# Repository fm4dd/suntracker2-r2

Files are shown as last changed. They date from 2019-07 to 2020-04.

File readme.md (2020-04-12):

# SunTracker2 Revision 2



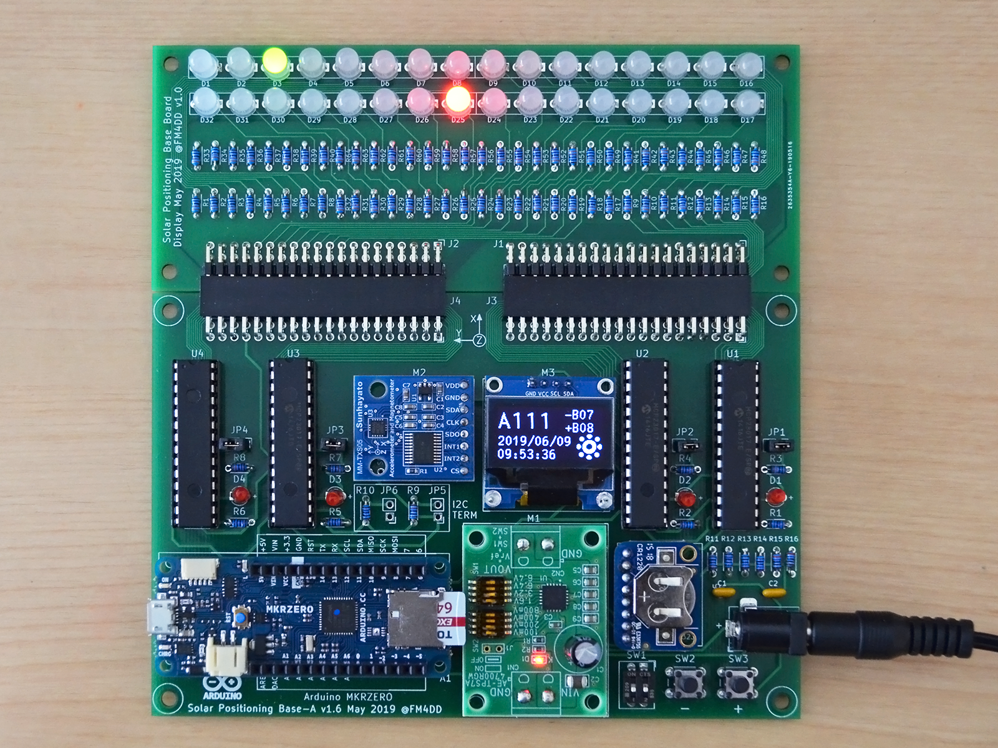
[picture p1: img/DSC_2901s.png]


This project develops a photovoltaic (PV) solar tracking controller.
Pictured above is the revision 2 prototype. PV solar trackers control the PV
panel direction to keep the panel perpendicular to the Sun, maximizing the
power output. The power output difference for a fully aligned panel is
reported to be in a range of 15~40%, which would be substantial.

## Design

The goal is a self-orienting dual-axis, scheduled, Arduino-based solar
tracker. I want to control PV panel orientation for both Elevation and
Azimuth angles (dual-axis), based on the calculated solar position of a PV
systems specific geographic location and time (scheduled).

Working under space, cost and time constraints, the prototype development is
done on a small scale model. Eventually, I want to control and optimize the
orientation of Mini-PV systems.

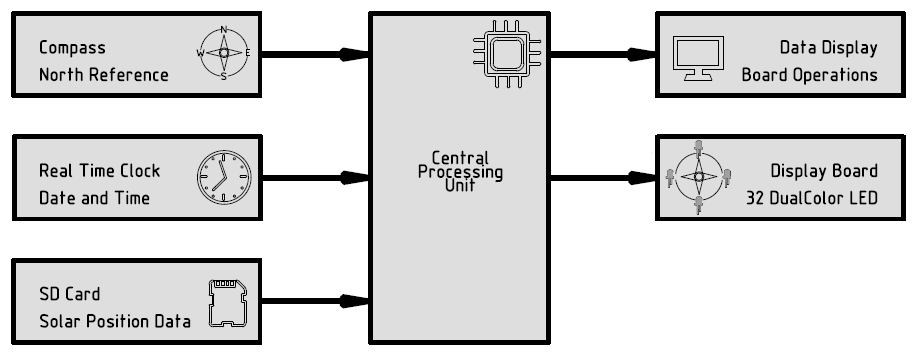
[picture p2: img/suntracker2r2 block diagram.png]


This is a interim revision to establish PCB design and manufacturing. The next
version is revision 3, located <a href="https://github.com/fm4dd/suntracker2-r3">here</a>

### Board Description and Components

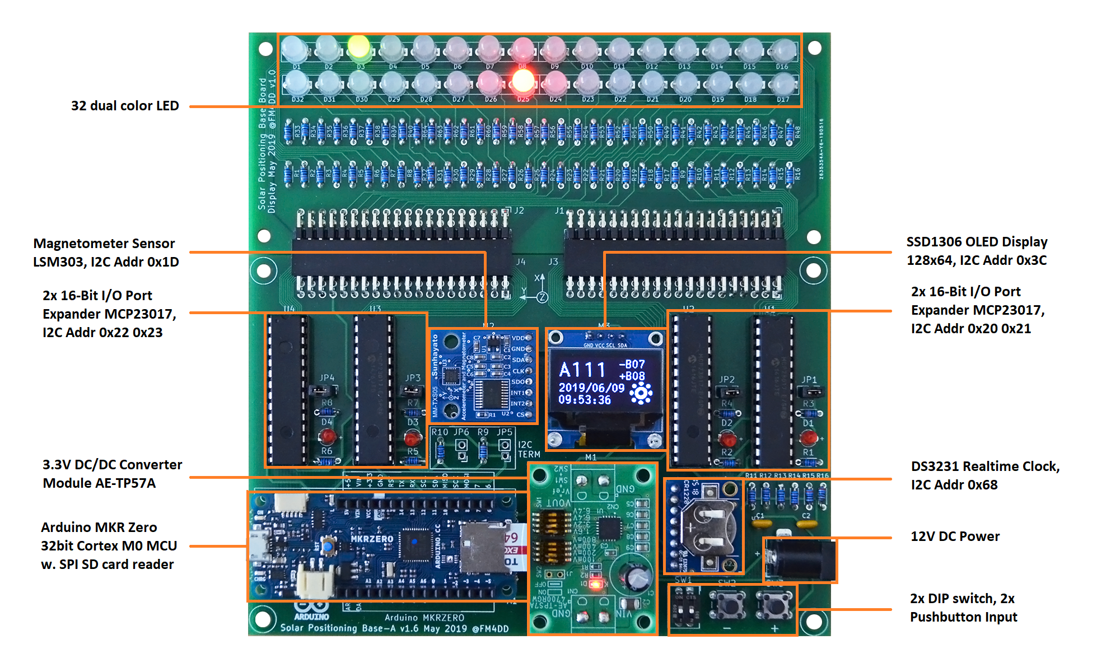
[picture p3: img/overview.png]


The main controller board contains the 32bit Arduino MKRZero MCU, the
LSM303 magnetometer sensor, DS3231 RTC clock module, and four 16pin GPIO expander
circuits. A 128x64 OLED display shows operational data and status messages.

A 32-color LED display board connects to the controller board to develop the 
GPIO controller functions for the sun positioning display.

In the next revision, the 32 LED ring will form a ring that represents the horizon
with north, sunrise and sunset indicators, and a green indicator to display the
suns daily movement over time.

The solar position data gets calculated off-system in advance, and saved into a
micro SD card. The pre-generated daily sun position files are then read by the
Arduino MKR Zero microcontroller through the onboard card reader. The
astronomical calculations of the suns position require sufficient CPU power, and
are taxing on Microcontrollers.

At the moment I am using a sun position dataset that covers two years of
operation, and uses approx. 20MB in size (46 MB with additional debug data). I
wrote the “suncalc” tool to pre-calculate the data set files for a specific
location, on a Linux PC.

### PCB

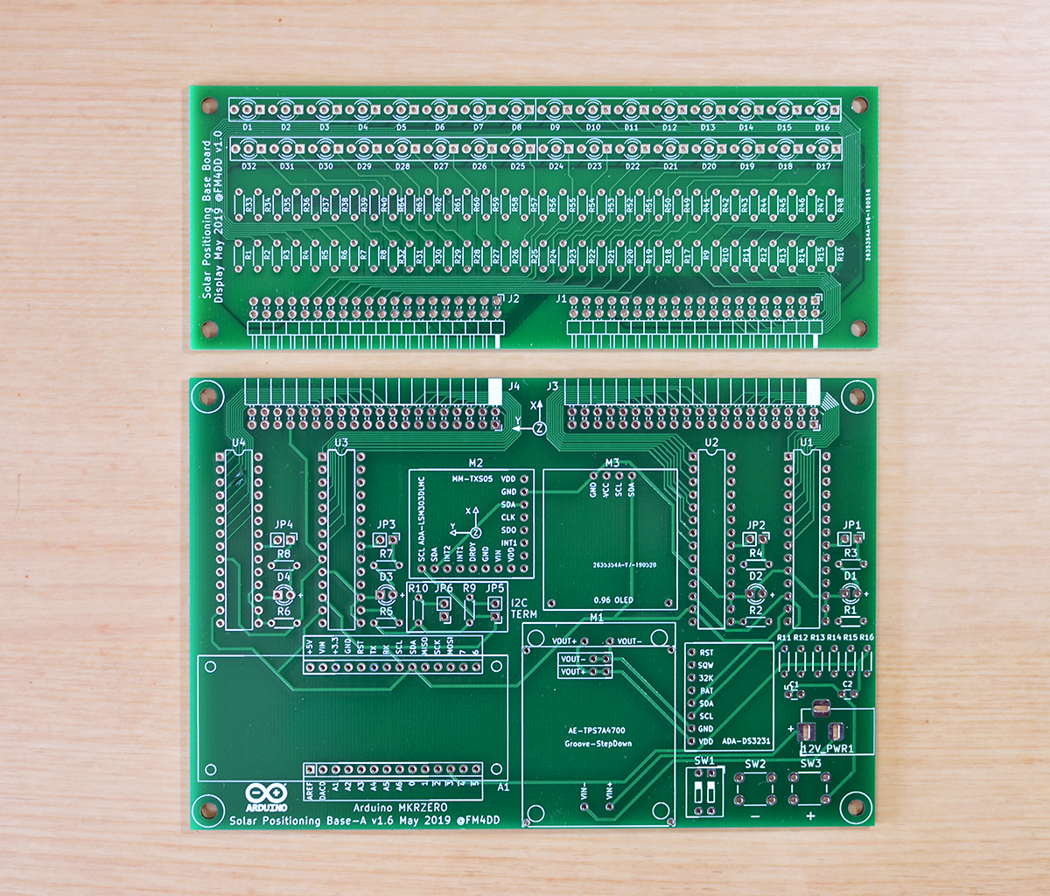
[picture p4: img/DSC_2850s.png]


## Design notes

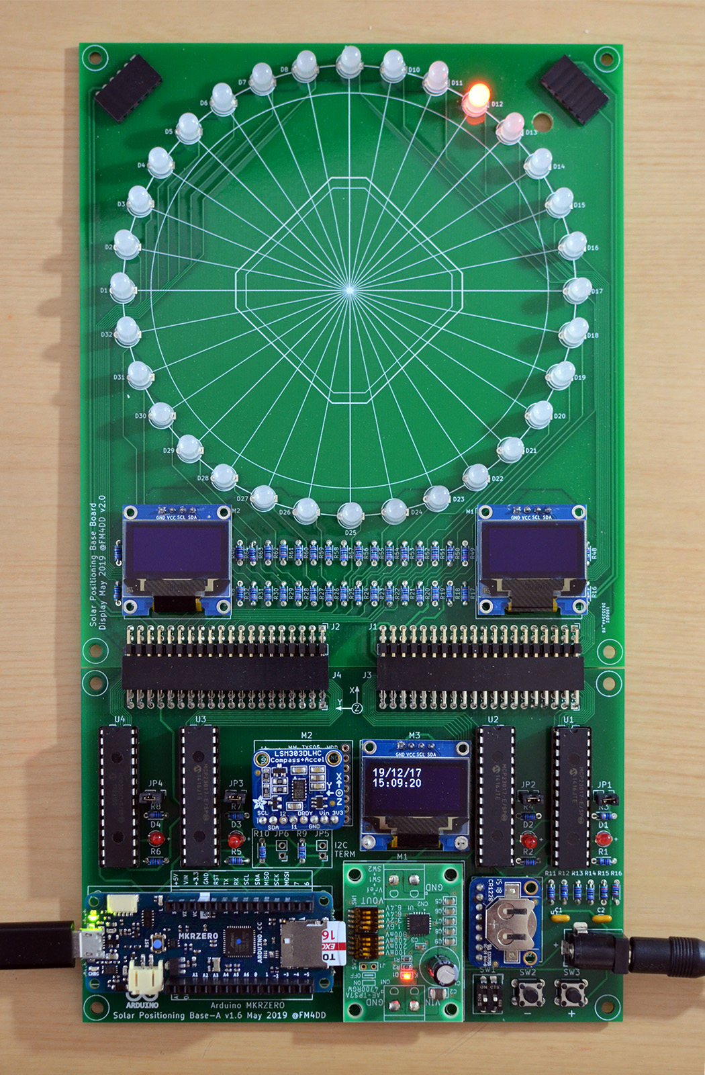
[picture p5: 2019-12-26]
img/displayv2-on-mbv16.jpg

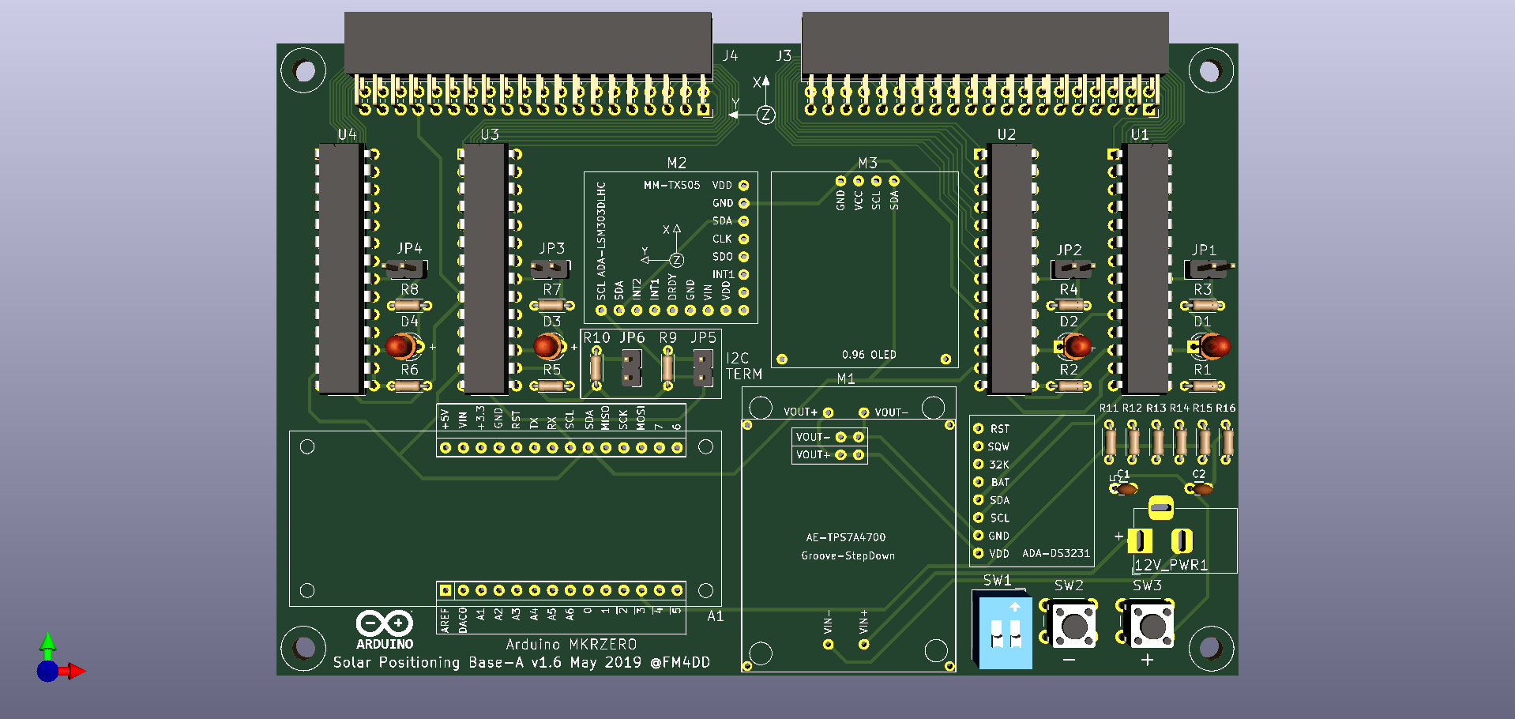
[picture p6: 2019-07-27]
img/mainboard v1.6.png

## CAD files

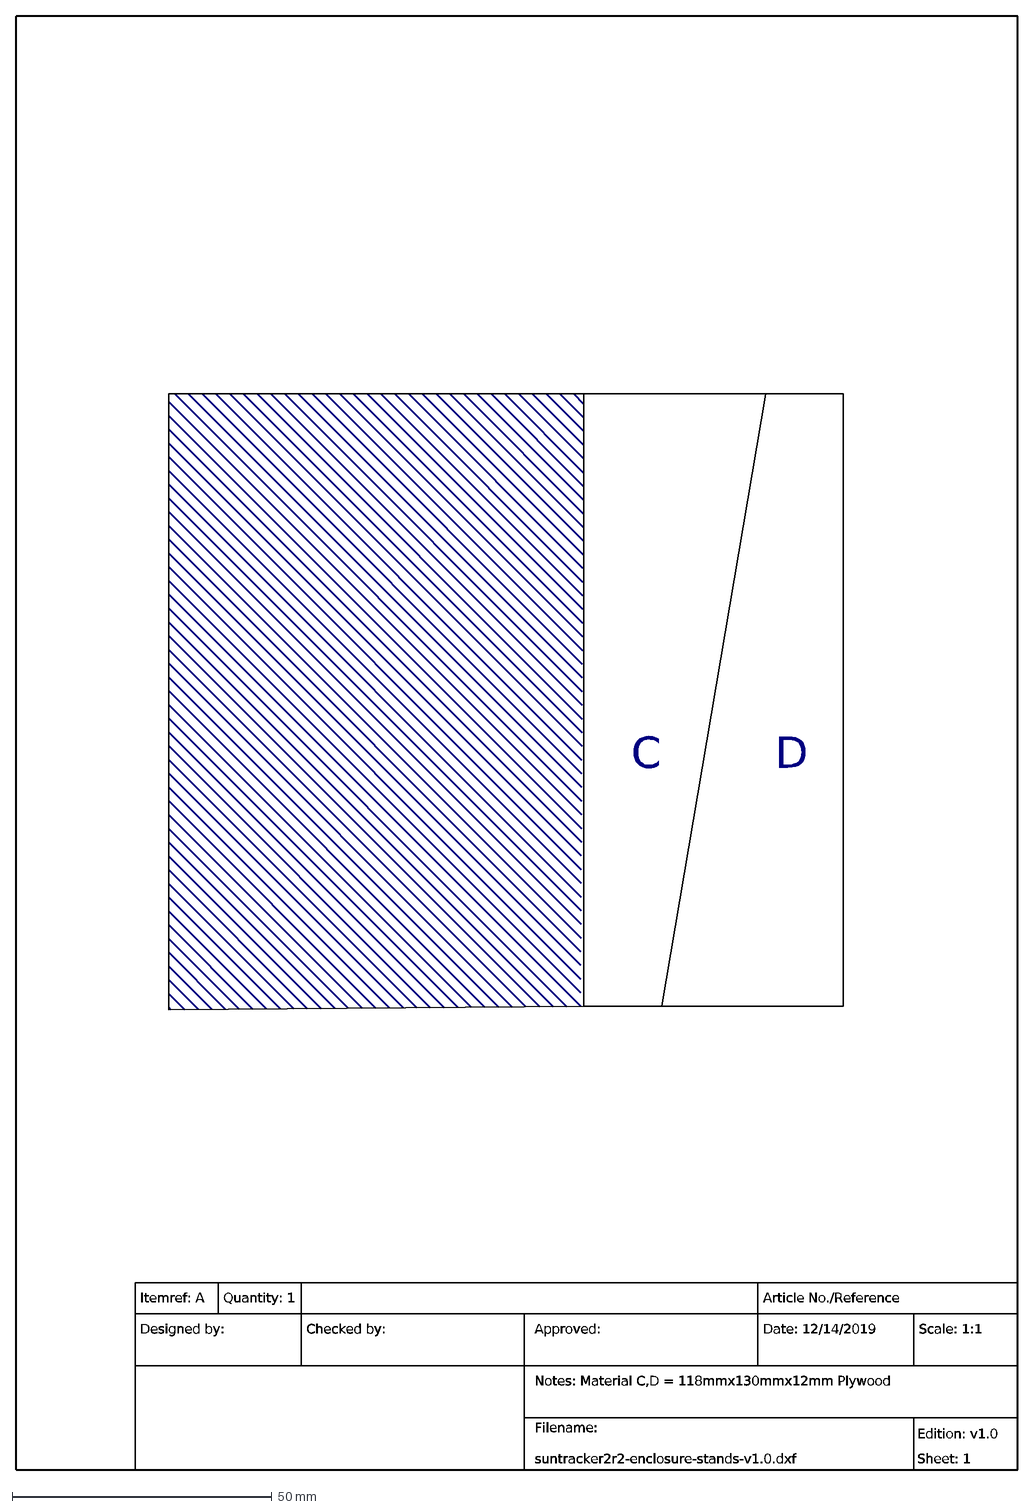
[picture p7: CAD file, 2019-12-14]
doc/20191214 suntracker2r4-enclosure-stands-v1.0.dxf
Notes: Material C,D = 118mmx130mmx12mm Plywood
Itemref: A
Quantity: 1
Article No./Reference
Designed by:
Checked by:
Approved:
Filename: suntracker2r2-enclosure-stands-v1.0.dxf
Date: 12/14/2019
Scale: 1:1
Edition: v1.0 Sheet: 1
C
D

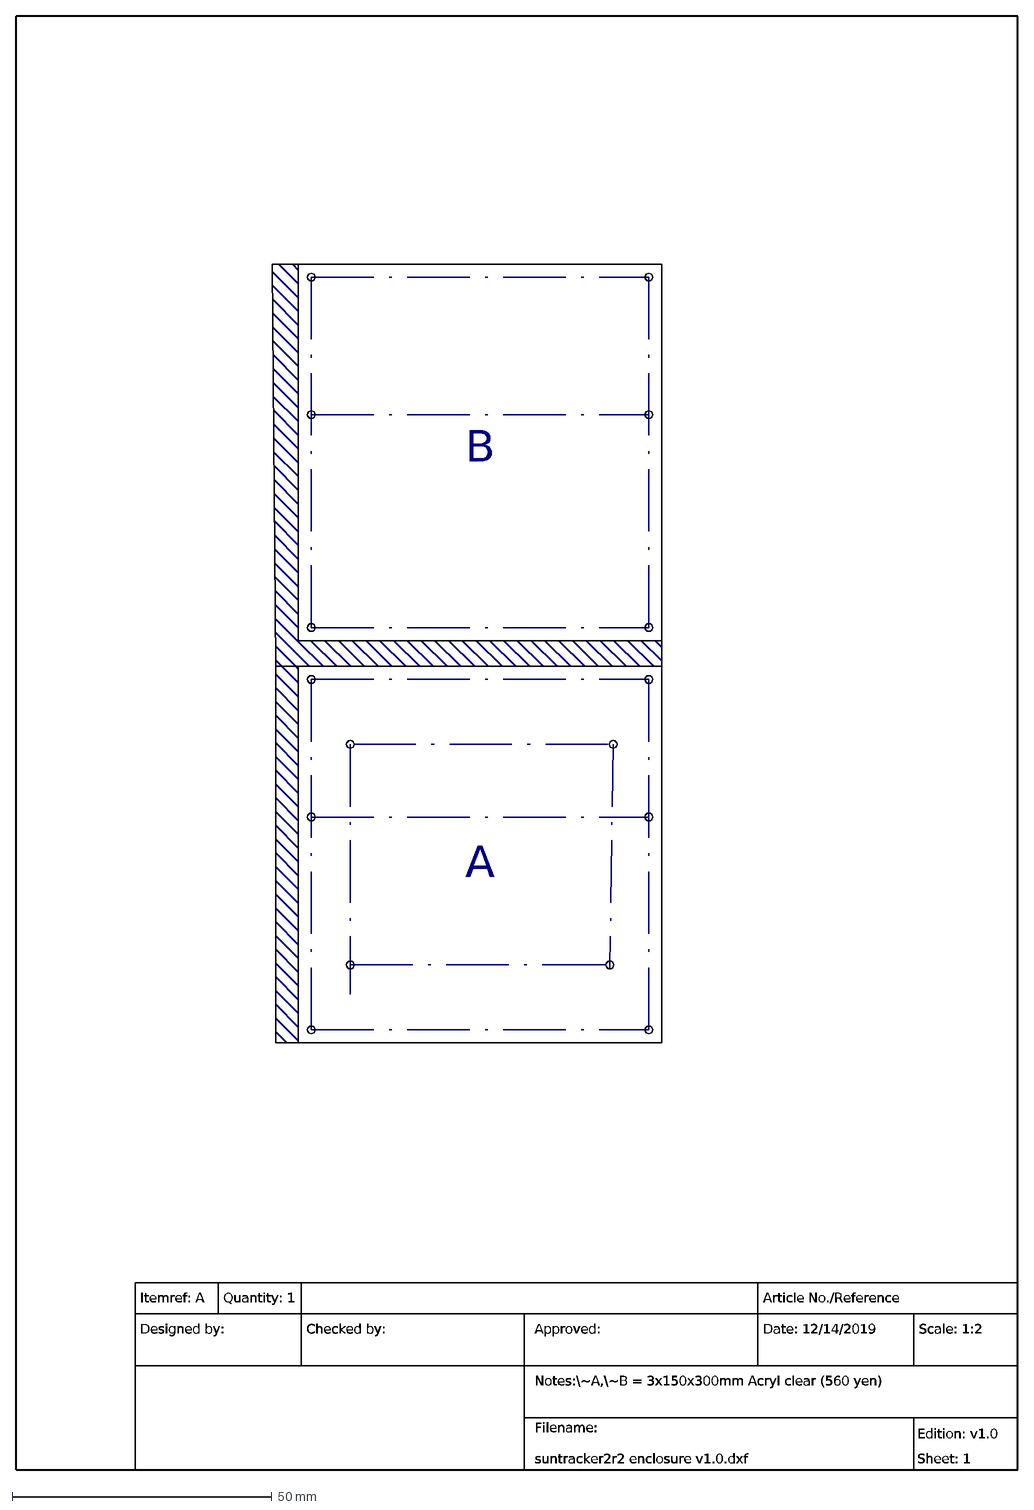
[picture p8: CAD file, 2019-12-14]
doc/20191214 Suntracker2r2 enclosure v1.0.dxf
Notes:\~A,\~B = 3x150x300mm Acryl clear (560 yen)
Itemref: A
Quantity: 1
Article No./Reference
Designed by:
Checked by:
Approved:
Filename: suntracker2r2 enclosure v1.0.dxf
Date: 12/14/2019
Scale: 1:2
Edition: v1.0 Sheet: 1
A
B

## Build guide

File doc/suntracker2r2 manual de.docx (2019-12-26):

Das Suntracker2R2 ist eine 32-bit Arduino MKR Zero basierte Mikroprozessor Entwicklungsumgebung zur Ansteuerung von 64 digitalen I/O. Damit kann man zum Beispiel eine Displayboard Erweiterung mit 32x Zweifarben-LED zur Datenausgabe ansteuern. Als Eingangsdaten steht eine Echtzeituhr (RTC), ein Magnetometer Sensor, und der MicroSD Kartenleser des Arduino MKR Zero zur Verfuegung. Ein 128x64 OLED Display dient zur Zustands-, Daten und Messwertausgabe.

## Board Design


## Komponenten Uebersicht

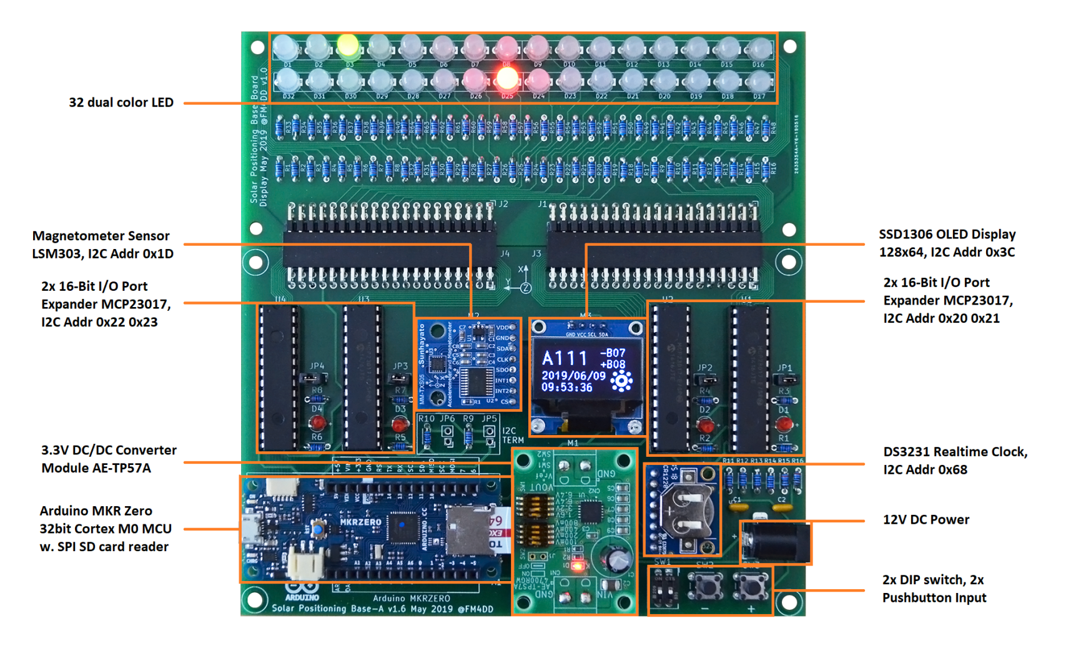
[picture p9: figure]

Below tables show some of the DE0-Nano-SOC’s basic built-in HW components: LED, Pushbutton, DIP, and Clock.

LED | FPGA PIN | | Push Button | FPGA PIN | | DIP Switch | FPGA PIN
LED[0] | PIN_W15 | | KEY[0] | PIN_AH17 | | DIP Switch[0] | PIN_L10
LED[1] | PIN_AA24 | | KEY[1] | PIN_AH16 | | DIP Switch[1] | PIN_L9
LED[2] | PIN_V16 | | | | | DIP Switch[2] | PIN_H6
LED[3] | PIN_V15 | | Clock | FPGA PIN | | DIP Switch[3] | PIN_H5
LED[4] | PIN_AF26 | | FPGA_CLK1_50 | PIN_V11
LED[5] | PIN_AE26 | | FPGA_CLK2_50 | PIN_Y13
LED[6] | PIN_Y16
LED[7] | PIN_AA23 | | Pushbutton keys are level “high”, and go “low” when pressed.
| | | DIP switches are level “high” in down position, and “low” when up.

## Arduino MKR Zero

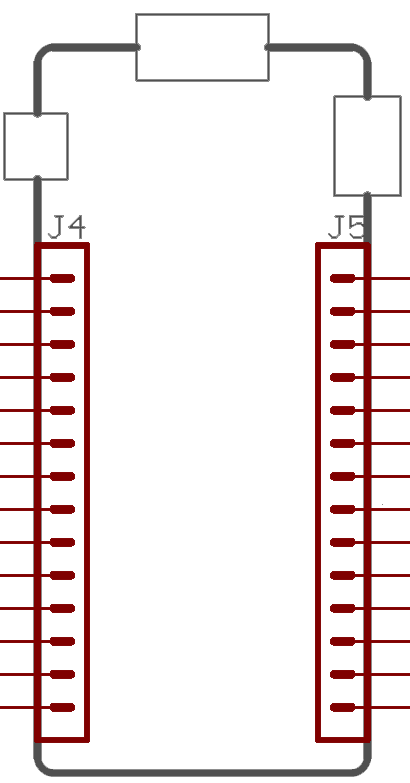
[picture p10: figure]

Herzstück des Boards ist der Arduino MKR Zero, eine Cortex M0 basierte 32bit CPU mit 32K RAM und 256K Flash Speicher.

I/O Header Pin Belegungsplan:

Am Arduino sind 8 Pins belegt,

und 20 von 28 Pins ungenutzt.

Board Pin | Arduino Pin | # | | # | Arduino Pin | Board Pin
N/A | AREF | 1 | | 28 | +5V | N/A
N/A | DAC0 | 2 | | 27 | VIN | N/A
N/A | A1 | 3 | | 26 | +3.3V | DC Converter +
N/A | A2 | 4 | | 25 | GND | DC Converter -
N/A | A3 | 5 | | 24 | RESET | N/A
N/A | A4 | 6 | | 23 | 14 | N/A
N/A | A5 | 7 | | 22 | 13 | N/A
N/A | A6 | 8 | | 21 | SCL | I2C Bus Clock
DIP Switch 0 | 0 | 9 | | 20 | SDA | I2C Bus Data
DIP Switch 1 | 1 | 10 | | 19 | 10 | N/A
Taster 1 (SW2) | 2 | 11 | | 18 | 9 | N/A
Taster 2 (SW3) | 3 | 12 | | 17 | 8 | N/A
N/A | 4 | 13 | | 16 | 7 | N/A
N/A | 5 | 14 | | 15 | 6 | N/A

## DIE DIp Schalter und Taster (Default OFF = 1, ON = 0)

Das Board ist mit zwei DIP Schaltern und zwei Tastern ausgestattet. Diese können zur Steuerung von Programmen und Ausgaben frei belegt werden. Der folgende Demo Sketch s2r2-dipkey-test.ino zeigt die Ansteuerung:

/* ------------------------------------------------- */

/* Suntracker2R2 DIP and Pushbutton Test Sketch */

/* ------------------------------------------------- */

#include "Arduino.h" // default library

#define DIP1 0 // dip switch 1 <-> IO-pin 0

#define DIP2 1 // dip switch 2 <-> IO-pin 1

#define KEY1 2 // pushbutton 1 <-> IO-pin 2

#define KEY2 3 // pushbutton 2 <-> IO-pin 3

uint8_t dippos1 = 1; // dip switch 1 position

uint8_t dippos2 = 1; // dip switch 2 position

uint8_t push1 = 1; // pushbutton 1 position

uint8_t push2 = 1; // pushbutton 2 position

void setup() {

Serial.begin(115200);

while (!Serial); // wait for serial port to connect.

Serial.println("Serial OK");

/* ------------------------------------------------- */

/* Set dip switch and push button IO pins for input */

/* ------------------------------------------------- */

pinMode(DIP1, INPUT);

pinMode(DIP2, INPUT);

pinMode(KEY1, INPUT);

pinMode(KEY2, INPUT);

pinMode(push1, INPUT);

pinMode(push2, INPUT);

Serial.println("DIP and KEY pins set for input.");

}

void loop() {

/* ------------------------------------------------- */

/* Get and display dip switch and pushbutton status */

/* ------------------------------------------------- */

Serial.print(" DIP1: "); dippos1 = digitalRead(DIP1); Serial.print(dippos1);

Serial.print(" DIP2: "); dippos2 = digitalRead(DIP2); Serial.print(dippos2);

Serial.print(" KEY1: "); push1 = digitalRead(KEY1); Serial.print(push1);

Serial.print(" KEY1: "); push2 = digitalRead(KEY2); Serial.print(push2);

Serial.println();

delay(500);

}

Die Ausgabe erfolgt hier über den seriellen Monitor der Arduino IDE. Dieser sollte in der Arduino IDE gestartet werden, sonst beginnt das Program nicht. Hier ist ein Beispiel-Screenshot der seriellen Ausgabe:

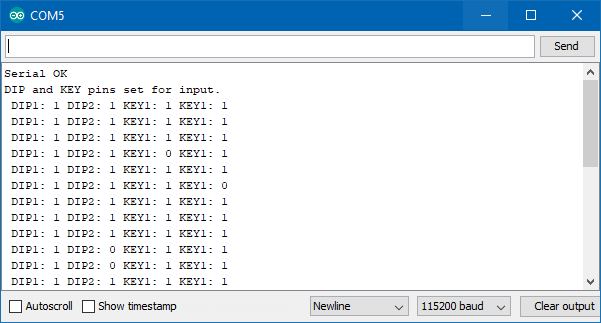
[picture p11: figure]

- Beachte die invertierte Logik: Ein Tastendruck oder Switch-ON generiert ein ‘0’ Signal.

## Der I2C BUS

Auf dem Mainboard verbindet der I2C Bus die acht folgenden Geraete mit der Arduino MCU:

# | Geraet | Typ | Hersteller | I2C Bus Addresse (Hex)

1 | Accelerometer | LSM303DLHC | Adafruit | 0x19
2 | Magnetometer | See above | See above | 0x1E
3 | IO Expander 1 | MCP23017 E/SP | Microchip | 0x20
4 | IO Expander 2 | MCP23017 E/SP | Microchip | 0x21
5 | IO Expander 3 | MCP23017 E/SP | Microchip | 0x22
6 | IO Expander 4 | MCP23017 E/SP | Microchip | 0x23
7 | OLED Display | SSD1306 | Unbranded | 0x3C
8 | RTC Clock | DS3231 | Adafruit | 0x68

Der Demo Sketch s2r2-i2cscan-test.ino ueberprüft, ob alle Gerate am I2C Bus gefunden werden:

/* ------------------------------------------------- */

/* Suntracker2R2 12C Bus Scanner Test Sketch */

/* ------------------------------------------------- */

#include <Wire.h> // Arduino built-in I2C bus function library

uint8_t error = 0; // I2C commuications error

uint8_t address = 0; // I2C device address

uint8_t counter = 0; // I2C device counter

void setup(){

Serial.begin(115200);

while (!Serial); // wait for serial port to connect.

Serial.println("Serial OK. Scanning I2C Bus:");

Wire.begin(); // enable I2C bus, default speed

for(address = 0; address < 127; address++ ) {

Serial.print(".");

Wire.beginTransmission(address);

error = Wire.endTransmission();

if (error == 0){

Serial.print("\nDevice found: 0x");

Serial.println(address,HEX);

counter++;

continue;

}

if (error == 4) {

Serial.print("\nDevice error: 0x");

Serial.println(address,HEX);

continue;

}

delay(100);

}

Serial.print("\n I2C bus scan result: ");

Serial.print(counter);

Serial.print(" devices found.");

}

void loop() {}

Serielle Ausgabe:

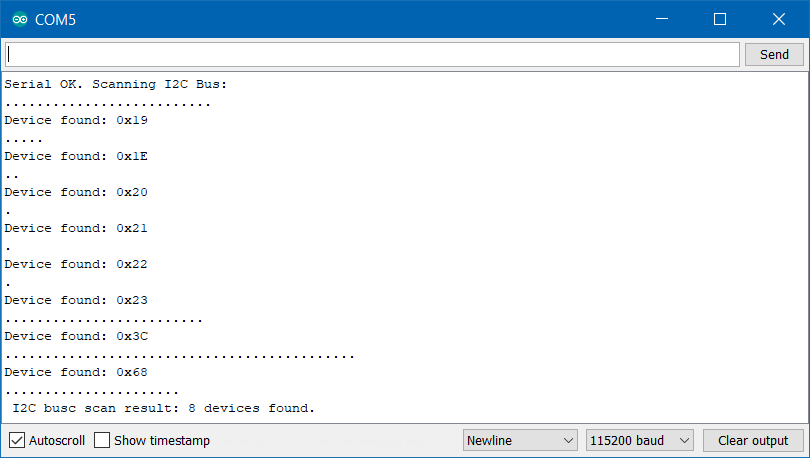
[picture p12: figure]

## Der IO Expander MCP23017

Der IO Expander Chip MCP23017 von Microchip stellt 16 digitale Pins via I2C Bus zur Verfügung. Diese IO Pins koennen als Input oder Output gesetzt werden. Durch drei Addressleitungen am Expander Chip kann man bis zu acht Expander an einem I2C Bus betreiben, und bekommt damit maximal 128 IO. Das Suntracker2 R2 Mainboard hat vier Expander (U1-U4), deren 64 IO Pins auf zwei 40-Pin Expansion Steckerleisten (J3, J4) gelegt sind. Zur optischen Statuskontrolle und zum schnellen Debug hat das Mainboard vier rote Status LEDs (D1-D4), die jeweils auf den ersten IO Pin des jeweiligen IO Expanders geschalten sind. Diese Status LED kann man bei Bedarf durch Entfernen von Jumper JP1-JP4 einzeln abschalten, um zum Beispiel diesen Pin auch als Input Pin betreiben zu können.

Durch Anstecken der optionalen Displayboard Erweiterung werden die 64 IO Pins vom Development Mainboard mit den 32 Zweifarben-LED (rot/grün) auf der Displayboard Erweiterung verbunden. Fuer die Displayboard Erweiterung werden dazu alle Pins der vier IO Expander im Output Mode betrieben.

Der Demo Sketch s2r2-mcp23017-test1.ino blinkt die rote Status LED (D1) des ersten IO Expanders (U1). Ist die Displayboard Erweiterung angeschlossen, blinkt auch die LED D1 des Displayboards in rot mit der Status LED mit.

/* ------------------------------------------------- */

/* Suntracker2R2 1. IO Expander MCP23017 Test Sketch */

/* ------------------------------------------------- */

#include <Wire.h> // Arduino built-in I2C bus function library

#include <Adafruit_MCP23017.h> // https://github.com/adafruit/Adafruit-MCP23017-Arduino-Library

Adafruit_MCP23017 mcp1; // create object for 1st MCP23017

void setup() {

Serial.begin(115200);

while (!Serial); // wait for serial port to connect.

Serial.println("Serial OK");

Wire.begin(); // enable I2c bus

mcp1.begin(); // enable 1st MCP23017 expander chip

mcp1.pinMode(0, OUTPUT); // set 1st expander pin-0 as output

mcp1.digitalWrite(0, LOW); // set 1st expander pin-0 to '0'

}

void loop() {

mcp1.digitalWrite(0, HIGH); // set 1st expander pin-0 to '1'

Serial.print("1st MCP23017 pin-0 state: ");

Serial.print(mcp1.digitalRead(0));

delay(500);

mcp1.digitalWrite(0, LOW); // set 1st expander pin-0 to '0'

Serial.print(" state: ");

Serial.println(mcp1.digitalRead(0));

delay(500);

}

Serielle Ausgabe:

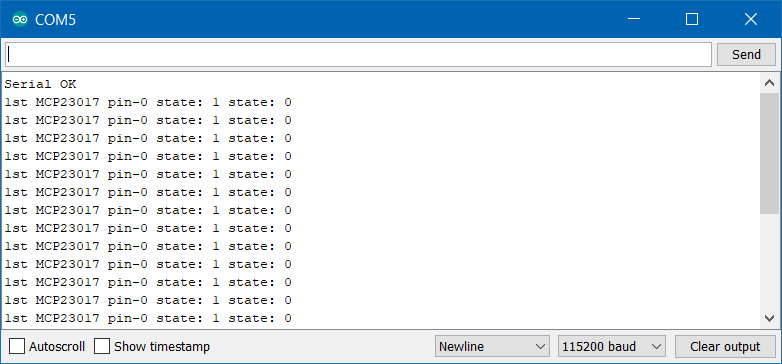
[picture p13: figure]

Achtung:

Zur Ansteuerung des MCP23017 benutzt dieser Demo Sketch eine externe Funktionsbibliothek für den MCP23017 Chip von Adafruit. Externe Bibliotheken werden in der Ardunio IDE durch den Menüpunkt “Tools” → “Manage Libraries” hinzugefuegt. Ist man mit dem Internet verbunden, gibt man unter diesem Menüpunkt im Suchfenster den Begriff “MCP23017” ein. Daraufhin sollten durch die Suche mehrere Bibliotheken vorgeschlagen werden. Eine davon ist die hier verwendete Bibliothek, erkennbar am Namen “Adafruit”. Diese installiert man vor dem Kompilieren des Sketches.

Aufgabe: Erstelle einen Sketch s2r2-key1led1-test.ino, worin das Drücken eines Pushbuttons die Status LED des ersten IO Expanders aufleuchten laesst. Kombiniere dazu Code aus dem Demo program s2r2-dipkey-test.ino mit dem Code aus dem Demo Program s2r2-mcp23017-test.ino.

Displayboard LED Belegungsplan:

# | IO Expander | LED Gruppe | Farbe

1 | U1 Pin 0-15 | D1-D16 (oben) | rot
2 | U2 Pin 0-15 | D17-D32 (unten) | rot
3 | U3 Pin 0-15 | D1-D16 (oben) | gruen
4 | U4 Pin 0-15 | D17-32 (unten) | gruen

Wenn man die weiteren 15 Pins des ersten IO Expanders als Output definiert, und dann auf ‘HIGH’ setzt, steuert man damit die 16 LED der oberen Reihe auf der Displayboard Erweiterung mit der Farbe rot an.

Ansteuerung von mehreren IO Expandern:

Das nächste Beispiel s2r2-mcp23017-test2.ino zeigt die Ansteuerung des vierten IO Expanders (U4). Durch Ihn schalten wir hier die untere LED Reihe (D17-32) der Displayboard Erweiterung mit grüner Farbe an.

/* ------------------------------------------------- */

/* Suntracker2R2 4. IO Expander MCP23017 Test Sketch */

/* ------------------------------------------------- */

#include <Wire.h> // Arduino built-in I2C bus function library

#include <Adafruit_MCP23017.h> // https://github.com/adafruit/Adafruit-MCP23017-Arduino-Library

Adafruit_MCP23017 mcp4; // create object for 4th MCP23017

uint8_t pin = 0; // pin counter to enable LED

void setup() {

Wire.begin(); // enable I2c bus

mcp4.begin(3); // enable 4th MCP23017 expander chip

for (pin = 0; pin<16; pin++) { // run through all 16 pins on the expander

mcp4.pinMode(pin, OUTPUT); // set expander pin as output

mcp4.digitalWrite(pin, HIGH); // set expander pin to '1' (LED ON)

}

}

void loop() {}

Das letzte Beispiel s2r2-mcp23017-test3.ino lässt die rote LED auf dem Displayboard im Kreis wandern:

/* ------------------------------------------------- */

/* Suntracker2R2 Wandering LED Test Sketch */

/* ------------------------------------------------- */

#include <Wire.h> // Arduino built-in I2C bus function library

#include <Adafruit_MCP23017.h> // https://github.com/adafruit/Adafruit-MCP23017-Arduino-Library

Adafruit_MCP23017 mcp1; // create object for 1st MCP23017

Adafruit_MCP23017 mcp2; // create object for 2nd MCP23017

uint8_t pin = 0; // pin counter to enable LED

uint8_t led = 0; // led counter

void setup() {

Wire.begin(); // enable I2c bus

mcp1.begin(0); // enable 1st MCP23017 expander chip

mcp2.begin(1); // enable 2nd MCP23017 expander chip

for (pin=0; pin<16; pin++) { // run through all 16 pins on the expander

mcp1.pinMode(pin, OUTPUT); // set expander pin as output

mcp1.digitalWrite(pin, LOW); // set expander pin to '0' (LED OFF)

mcp2.pinMode(pin, OUTPUT); // set expander pin as output

mcp2.digitalWrite(pin, LOW); // set expander pin to '0' (LED OFF)

}

}

void loop() {

for (led=0; led<32; led++) { // run through all 32 led

if(led < 16) { // for led 0-15, work on mcp1

pin = led; // pin number equals led

mcp1.digitalWrite(pin, HIGH); // set expander pin to '1' (LED ON)

if(pin == 0) // if we are on pin 0

mcp2.digitalWrite(15, LOW); // turn off the last LED on mcp2

else

mcp1.digitalWrite(pin-1, LOW); // turn off the previous LED

}

else { // we are on led 16 or above

pin = led-16; // pin number equals led minus 16

mcp2.digitalWrite(pin, HIGH); // set expander pin to '1' (LED ON)

if(pin == 0) // if we are on pin 0

mcp1.digitalWrite(15, LOW); // turn off the last LED on mcp1

else

mcp2.digitalWrite(pin-1, LOW); // turn off the previous LED

}

delay(60);

}

}

## Das OLED Display Mit TextAUSGABE

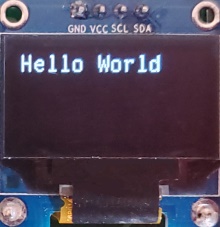
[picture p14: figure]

Das monochrome OLED Display hat eine Aufloesung von 128x64 Pixel. Es hat eine prima Leuchtstärke und ist mit einer passenden Bibliothek relativ einfach anzusteuern. Der Grafik-Chip ist ein SSD1306 von SOLOMON SYSTECH. Das Display wird ebenfalls ueber den I2C Bus angesprochen, unter der I2C Addresse 0x3C.

Zur Programmierung verwende ich die U8G2 Bibliothek von Oli Kraus. Die Dokumentation gibt es unter https://github.com/olikraus/u8g2.

Beim Installieren der Bibliothek (Ardunio IDE, “Tools” → “Manage Libraries”) wird auch eine Reihe von Demo Sketches bereitgestellt. Hier ist eine verkürzte Variante für den schnellen Erfolg zum Anzeigen von “Hello World”.

Der Beispielsketch s2r2-display-test.ino schreibt “Hello World” auf das Display:

/* ------------------------------------------------- */

/* Suntracker2R2 4SSD1306 OLED Display Test Sketch */

/* ------------------------------------------------- */

#include <Arduino.h> // Arduino default library

#include <U8g2lib.h> // https://github.com/olikraus/u8g2

U8G2_SSD1306_128X64_NONAME_F_HW_I2C oled1(U8G2_R0);

void setup() {

oled1.begin();

oled1.setFont(u8g2_font_t0_17_mr);

oled1.drawStr(0, 14, "Hello World");

oled1.sendBuffer();

}

void loop() {}

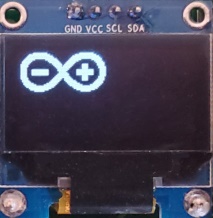
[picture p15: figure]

## Das OLED Display Mit GrafikAUSGABE

Das Display kann auch wunderbar Pixelgrafiken anzeigen. Dazu müssen wir aber erstmal eine geignete Bilddatei in das unterstützte XBPM (.xbm) Format umwandeln. Es gibt verschiedene Online Konvertierseiten und Tools dafür. Hier zum Beispiel unter der URL https://onlineconvertfree.com/convert-format/bmp-to-xbm/

Der Beispielsketch s2r2-graphic-test.ino zeigt das Arduino Logo:

/* ------------------------------------------------- */

/* Suntracker2R2 4SSD1306 OLED Graphics Test Sketch */

/* ------------------------------------------------- */

#include <Wire.h>

#include <U8g2lib.h> // https://github.com/olikraus/u8g2

U8G2_SSD1306_128X64_NONAME_F_HW_I2C oled1(U8G2_R0);

// 'arduino logo', 64x32px

static const unsigned char myLogo[] U8X8_PROGMEM = {

0x00, 0x00, 0x00, 0x00, 0x00, 0x00, 0x00, 0x00, 0x00, 0x00, 0x00, 0x00,

0x00, 0x00, 0x00, 0x00, 0x00, 0xFC, 0x0F, 0x00, 0x00, 0xF0, 0x3F, 0x00,

0x80, 0xFF, 0x3F, 0x00, 0x00, 0xFE, 0xFF, 0x00, 0xC0, 0xFF, 0xFF, 0x00,

0x80, 0xFF, 0xFF, 0x03, 0xE0, 0xFF, 0xFF, 0x01, 0xC0, 0xFF, 0xFF, 0x07,

0xF0, 0x07, 0xF8, 0x07, 0xE0, 0x1F, 0xE0, 0x0F, 0xF8, 0x01, 0xE0, 0x0F,

0xF0, 0x07, 0x80, 0x0F, 0xFC, 0x00, 0xC0, 0x1F, 0xF8, 0x01, 0x00, 0x1F,

0x7C, 0x00, 0x00, 0x3F, 0xFC, 0x00, 0x00, 0x3E, 0x3E, 0x00, 0x00, 0x7E,

0x7E, 0xC0, 0x03, 0x3E, 0x3E, 0x00, 0x00, 0x7C, 0x3F, 0xC0, 0x03, 0x3C,

0x1E, 0x00, 0x00, 0xF8, 0x1F, 0xC0, 0x03, 0x7C, 0x1E, 0x00, 0x00, 0xF0,

0x0F, 0xC0, 0x03, 0x78, 0x1E, 0xFE, 0x1F, 0xF0, 0x07, 0xFC, 0x3F, 0x78,

0x1E, 0xFE, 0x1F, 0xE0, 0x03, 0xFC, 0x3F, 0x78, 0x1E, 0xFE, 0x1F, 0xE0,

0x07, 0xFC, 0x3F, 0x78, 0x1E, 0xFE, 0x1F, 0xF0, 0x0F, 0xFC, 0x3F, 0x78,

0x1E, 0x00, 0x00, 0xF8, 0x0F, 0xC0, 0x03, 0x78, 0x1E, 0x00, 0x00, 0xFC,

0x1F, 0xC0, 0x03, 0x3C, 0x3E, 0x00, 0x00, 0x7E, 0x3E, 0xC0, 0x03, 0x3C,

0x3C, 0x00, 0x00, 0x3F, 0x7E, 0xC0, 0x03, 0x3E, 0x7C, 0x00, 0x80, 0x1F,

0xFC, 0x01, 0x00, 0x1F, 0xF8, 0x00, 0xC0, 0x0F, 0xF8, 0x03, 0x80, 0x1F,

0xF8, 0x03, 0xF0, 0x07, 0xF0, 0x0F, 0xC0, 0x0F, 0xF0, 0x0F, 0xFC, 0x03,

0xE0, 0x3F, 0xF0, 0x07, 0xE0, 0xFF, 0xFF, 0x01, 0x80, 0xFF, 0xFF, 0x03,

0x80, 0xFF, 0x7F, 0x00, 0x00, 0xFF, 0xFF, 0x01, 0x00, 0xFF, 0x1F, 0x00,

0x00, 0xFC, 0x7F, 0x00, 0x00, 0xF8, 0x03, 0x00, 0x00, 0xE0, 0x0F, 0x00,

0x00, 0x00, 0x00, 0x00, 0x00, 0x00, 0x00, 0x00, 0x00, 0x00, 0x00, 0x00,

0x00, 0x00, 0x00, 0x00, };

void setup() {

Wire.begin(); /* Enable I2C bus library */

oled1.begin(); /* Enable the OLED module */

oled1.clearDisplay();

oled1.drawXBMP(0,0, 64, 32, myLogo);

oled1.sendBuffer();

}

void loop() {}

## Die EchtzeitUHR DS3231

Die Echtzeituhr bekommt die Zeit einmal eingestellt, und mittels der 1220 Knopfbatterie wird die Zeit ständig aktualisiert. Der Arduino holt sich dann diese Zeit mittels Abfragen ueber den I2C Bus zur Geräteadresse der Uhr. Diese wird unter 0x68 angesprochen. Für das Uhrmodul gibt es mehrere Bibliotheken. Ich benutze die uRTCLib, deren Urpsrung sich hier befindet: https://github.com/Naguissa/uRTCLib

Der Beispielsketch s2r2-ds3231-test.ino zeigt wie man die Zeit setzt, abruft und auf das OLED displaz schreibt:

/* ------------------------------------------------- */

/* Suntracker2R2 DS3231 Realtime Clock Test Sketch */

/* ------------------------------------------------- */

#include <Arduino.h>

#include "uRTCLib.h" // https://github.com/Naguissa/uRTCLib

#include <U8g2lib.h> // https://github.com/olikraus/u8g2

U8G2_SSD1306_128X64_NONAME_F_HW_I2C oled1(U8G2_R0);

uRTCLib rtc; // realtime clock object

char lineStr[15]; // display output buffer, 14-chars + \0

void setup() {

Wire.begin(); // enable I2C bus

rtc.set_rtc_address(0x68); // Enable realtime clock

rtc.set_model(URTCLIB_MODEL_DS3231);

// rtc.set sec,min,hour,dayOfWeek,dayOfMonth,month,year

// to set the time, enable the line below

//rtc.set(0, 51, 0, 0, 16, 6, 19);

oled1.begin(); // enable oled display

oled1.setFont(u8g2_font_t0_17_mr);

}

void loop() {

rtc.refresh(); // get new time from clock

snprintf(lineStr, sizeof(lineStr), "%d/%02d/%02d", rtc.year(),rtc.month(),rtc.day());

oled1.drawStr(0, 15, lineStr);

snprintf(lineStr, sizeof(lineStr), "%02d:%02d:%02d", rtc.hour(),rtc.minute(),rtc.second());

oled1.drawStr(0, 30, lineStr);

oled1.sendBuffer(); // update oled display

}

## DER MAgnetSENSOR

Der Magnetsensor (Magnetometer) ist ein LSM303DLHC Modul von Adafruit. Er misst das Magnetfeld der Erde über drei Achsen. Das Erdmagnetfeld ist einerseits sehr schwach, und an jedem Ort unterschiedlich ausgeprägt. Deswegen erreicht man gute Ergebnisse nur mit Kalibrierung des Sensors, wobei er speziell auf die örtlichen Gegebenheiten eingestellt wird. Ich benutze hier nicht die Adafruit Bibliothek, sondern die Version von Pololu.

https://github.com/pololu/lsm303-arduino

Der Beispielsketch s2r2-lsm303-test.ino zeigt wie man eine Richtungsanzeige (Heading) abruft:

/* ------------------------------------------------- */

/* Suntracker2R2 LSM303 Magnetometer Test Sketch */

/* ------------------------------------------------- */

#include <Wire.h>

#include <LSM303.h>

LSM303 compass;

void setup() {

Serial.begin(115200);

while (!Serial); // wait for serial port to connect.

Serial.println("Serial OK");

Wire.begin();

compass.init();

compass.enableDefault();

/* Default Calibration values of +/-32767 for each axis */

compass.m_min = (LSM303::vector<int16_t>){-32767, -32767, -32767};

compass.m_max = (LSM303::vector<int16_t>){+32767, +32767, +32767};

}

void loop() {

compass.read();

float heading = compass.heading();

Serial.println(heading);

delay(100);

}

Serielle Ausgabe:

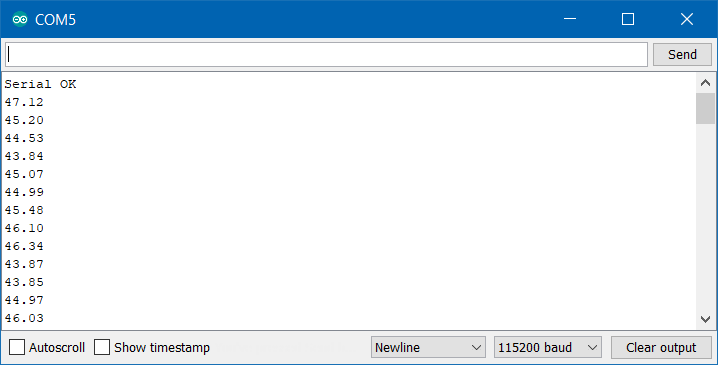
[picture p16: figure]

Zur Sensor Kalibrierung verwende ich einfach den mitgelieferten Beispielsketch unter “File” → “Examples” →”LSM303” → “Calibrate”. Mit den dabei ermittelten Werten ersetzt man dann die default Werte von 32767.

## DER Micro-SD KartenLESER

Der in das Arduino Board eingebaute Micro-SD Karteneinschub ist das einzige Gerät was nicht ueber den I2C Bus angesprochen wird. Es benutzt stattdessen den SPI Bus. Mit dem Kartenleser kann man normale FAT16 und FAT32 formatierte Mico SD Karten mit kleinen Einschränkungen Lesen und Schreiben. Die Bibliothek ist diesmal schon mit der Arduino IDE dabei, man muss sie nur im Programm einbinden.

Der Beispielsketch s2r2-sdcard-test.ino zeigt die gespeicherten Files auf der Karte an:

/* ------------------------------------------------- */

/* Suntracker2R2 MKR Zero SD Kartenleser Test Sketch */

/* ------------------------------------------------- */

#include <SPI.h>

#include <SD.h>

File root;

void setup() {

Serial.begin(115200);

while (!Serial); // wait for serial port to connect.

Serial.println("Serial OK");

Serial.print("Initializing SD card...");

if (!SD.begin(SDCARD_SS_PIN)) {

Serial.println("initialization failed!");

while(1);

}

Serial.println("initialization done.");

root = SD.open("/");

printDirectory(root, 0);

Serial.println("done!");

}

void loop() {}

void printDirectory(File dir, int numTabs) {

while (true) {

File entry = dir.openNextFile();

if (! entry) break; // no more files

for (uint8_t i = 0; i < numTabs; i++) {

Serial.print('\t');

}

Serial.print(entry.name());

if (entry.isDirectory()) {

Serial.println("/");

printDirectory(entry, numTabs + 1);

} else { // show file size

Serial.print("\t\t");

Serial.println(entry.size(), DEC);

}

entry.close();

}

}

Serielle Ausgabe:

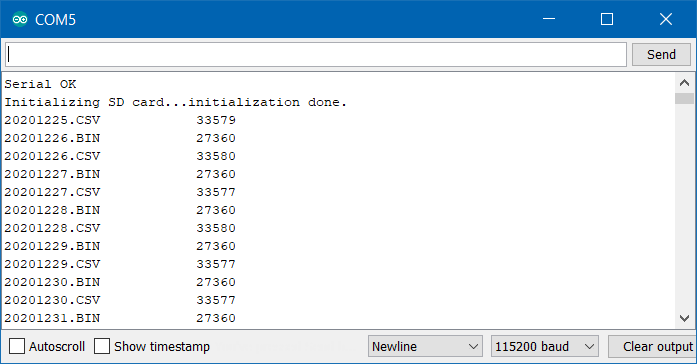
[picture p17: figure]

## Weitere Informationen

Mit den Komponenten auf dem Mainboard und dem Displayboard kann man zum Beispiel einen Kompass bauen, LED Muster erzeugen, oder die Uhrzeit anzeigen. Mit dem 2x40 Pin Erweiterungskartensteckplatz kann man andere Erweiterungskarten entwickeln, und so andere digitale Module einzubinden. Diese können sowohl Dateninput liefern, oder den Output vom Arduino verarbeiten. Auf dem Mainboard sind die meisten Module gesockelt, dadurch kann man Sie einfach ersetzen oder woanders weiterverwenden.

Die Leiterplatten und Schaltplaene des Mainboards und des Displayboards sind frei auf Github verfügbar unter: https://github.com/fm4dd/suntracker2-r2

Viel Spass!

12/14/2019 Suntracker2 R2 Manual Version 1.0 10

Suntracker2R2 Development Board Manual

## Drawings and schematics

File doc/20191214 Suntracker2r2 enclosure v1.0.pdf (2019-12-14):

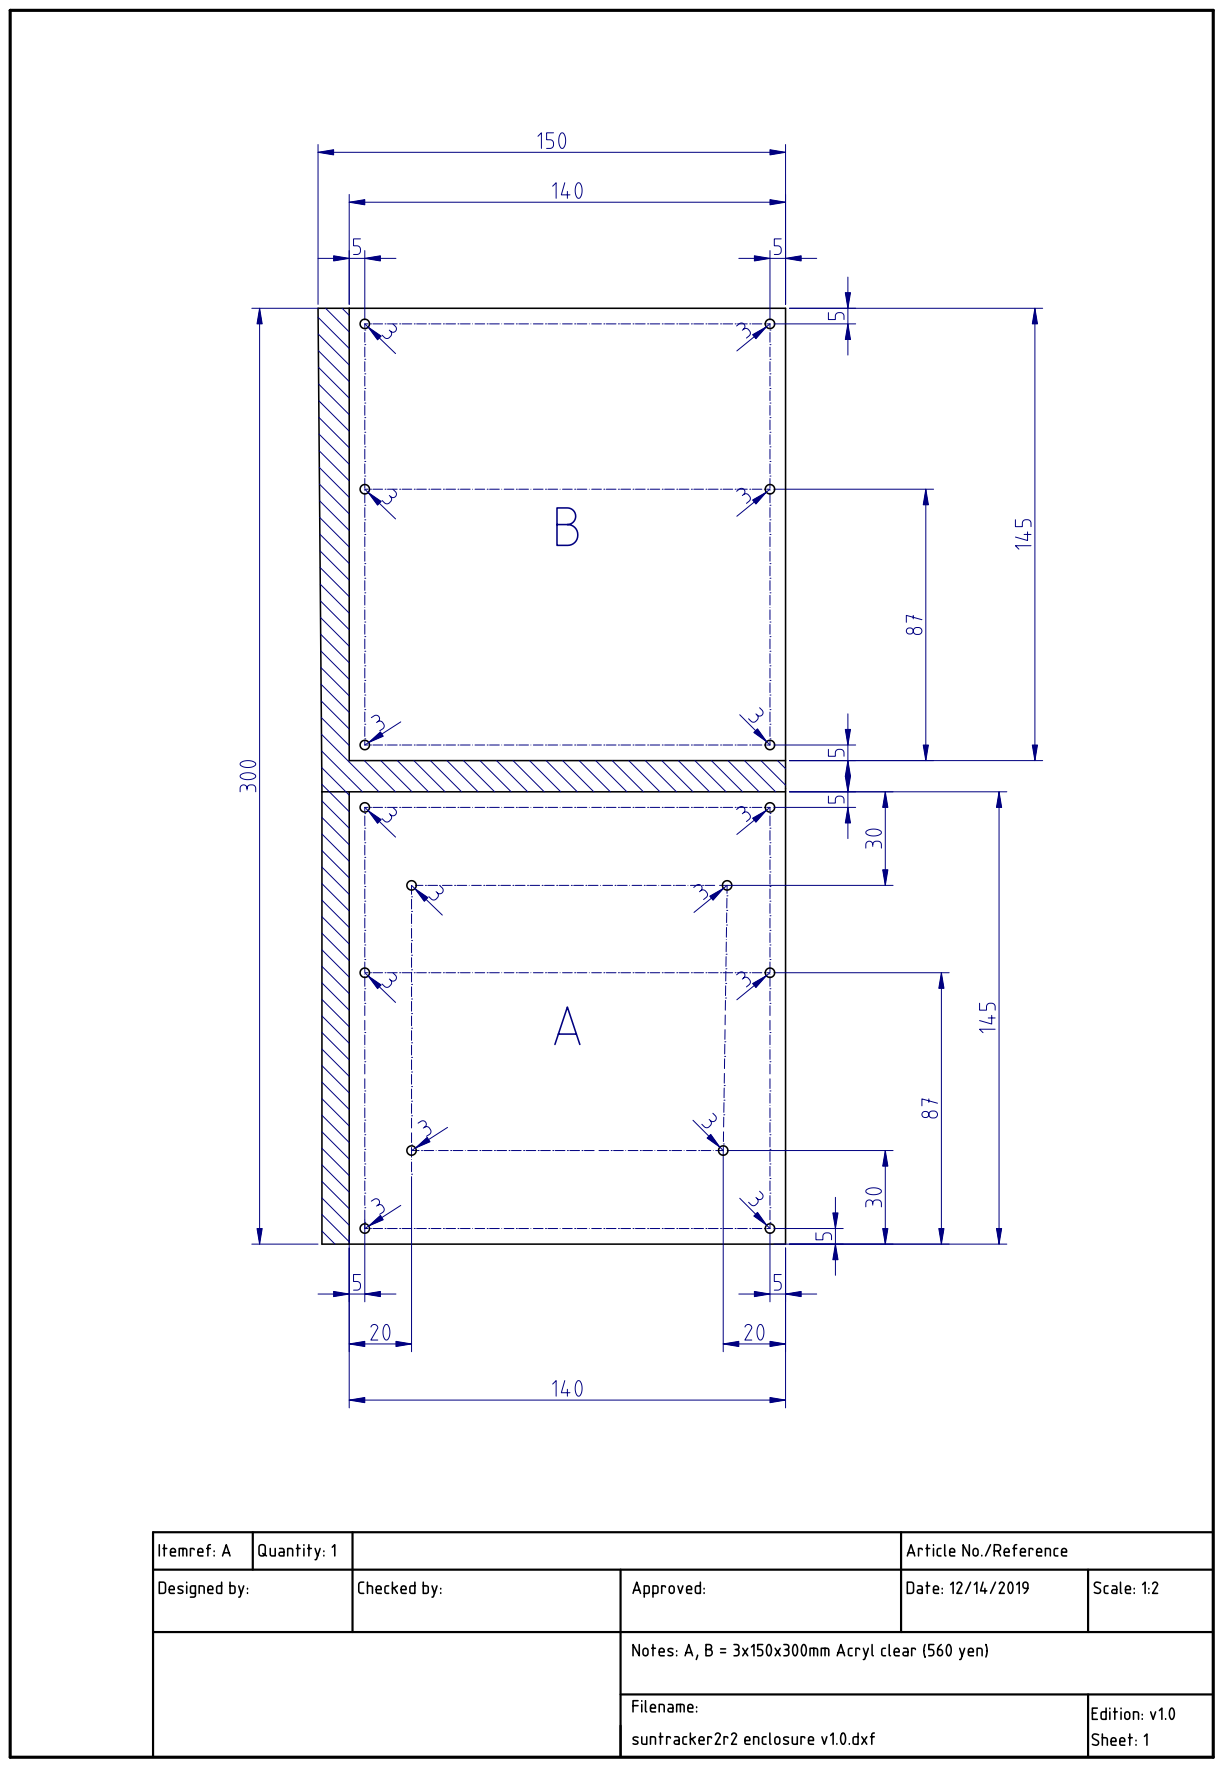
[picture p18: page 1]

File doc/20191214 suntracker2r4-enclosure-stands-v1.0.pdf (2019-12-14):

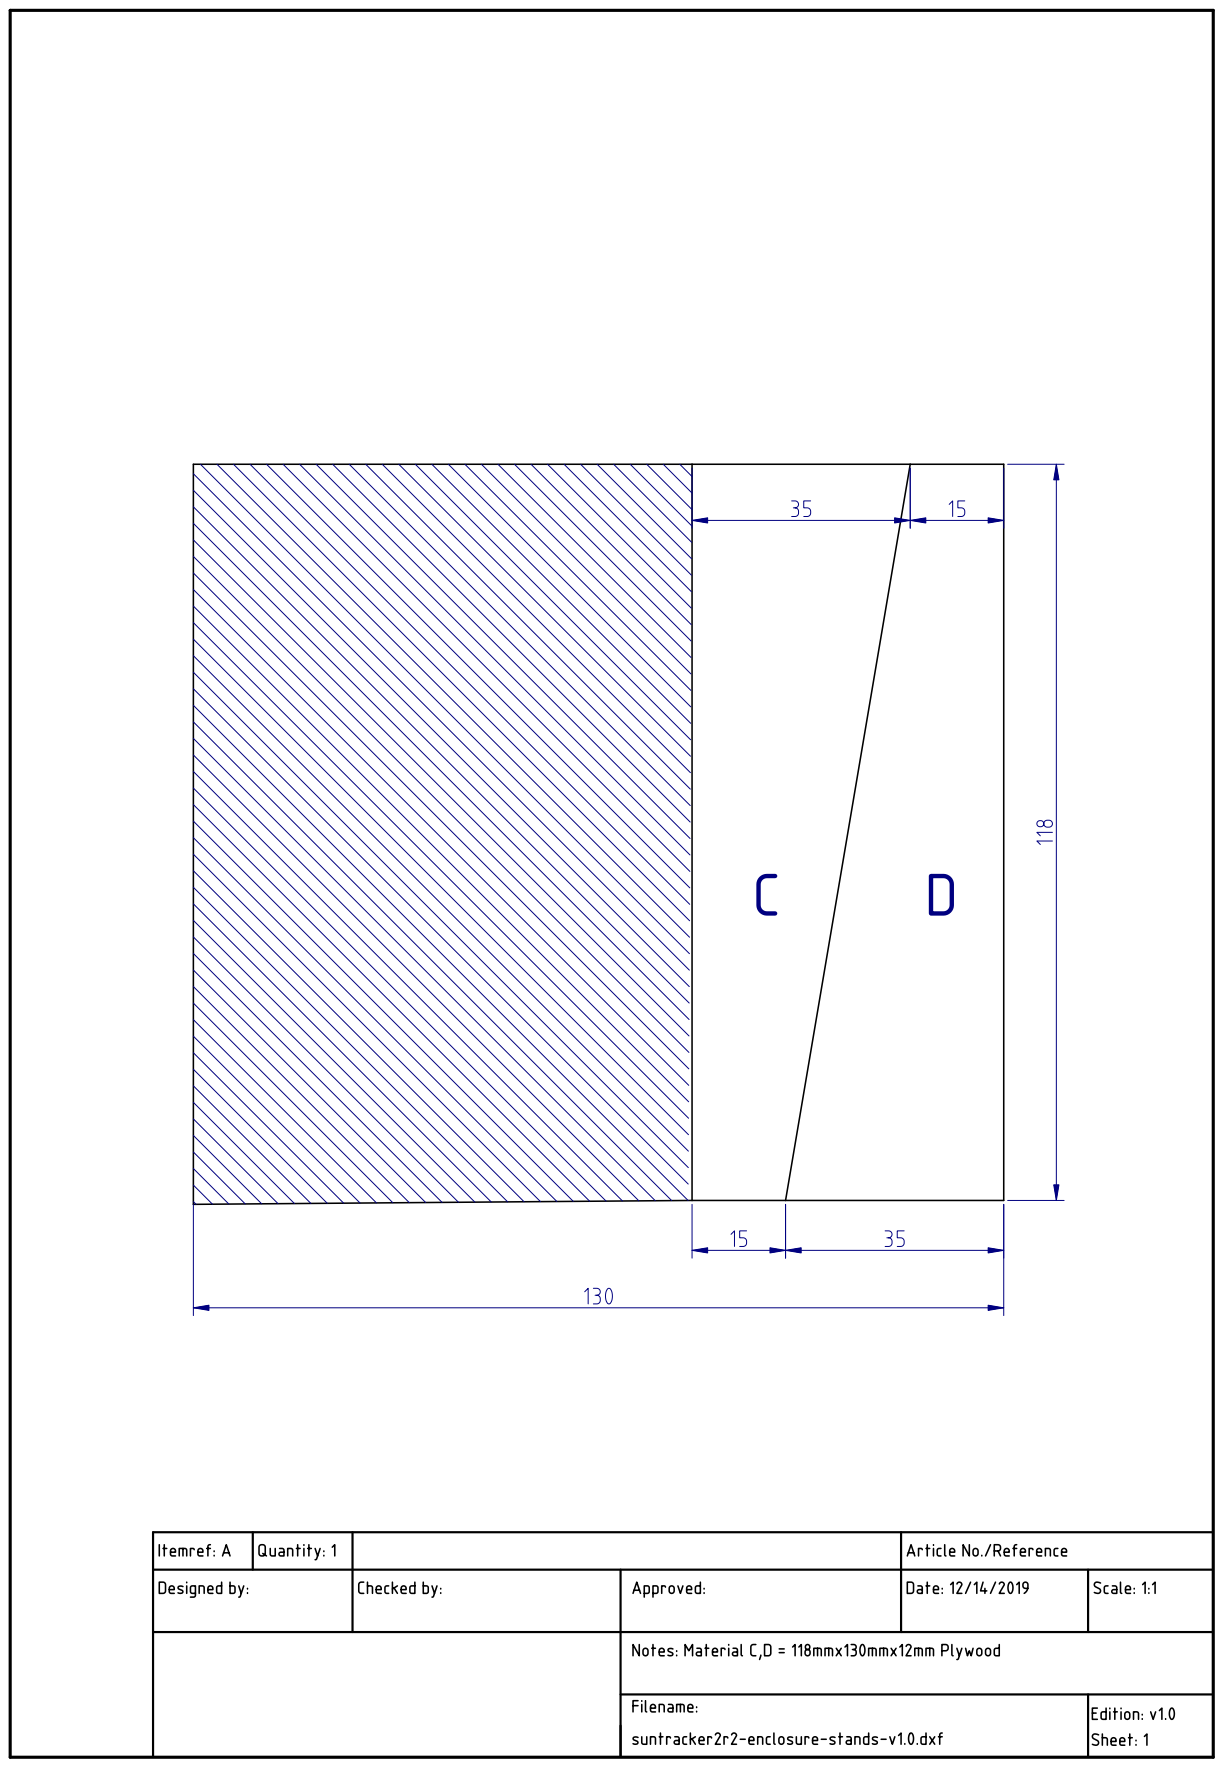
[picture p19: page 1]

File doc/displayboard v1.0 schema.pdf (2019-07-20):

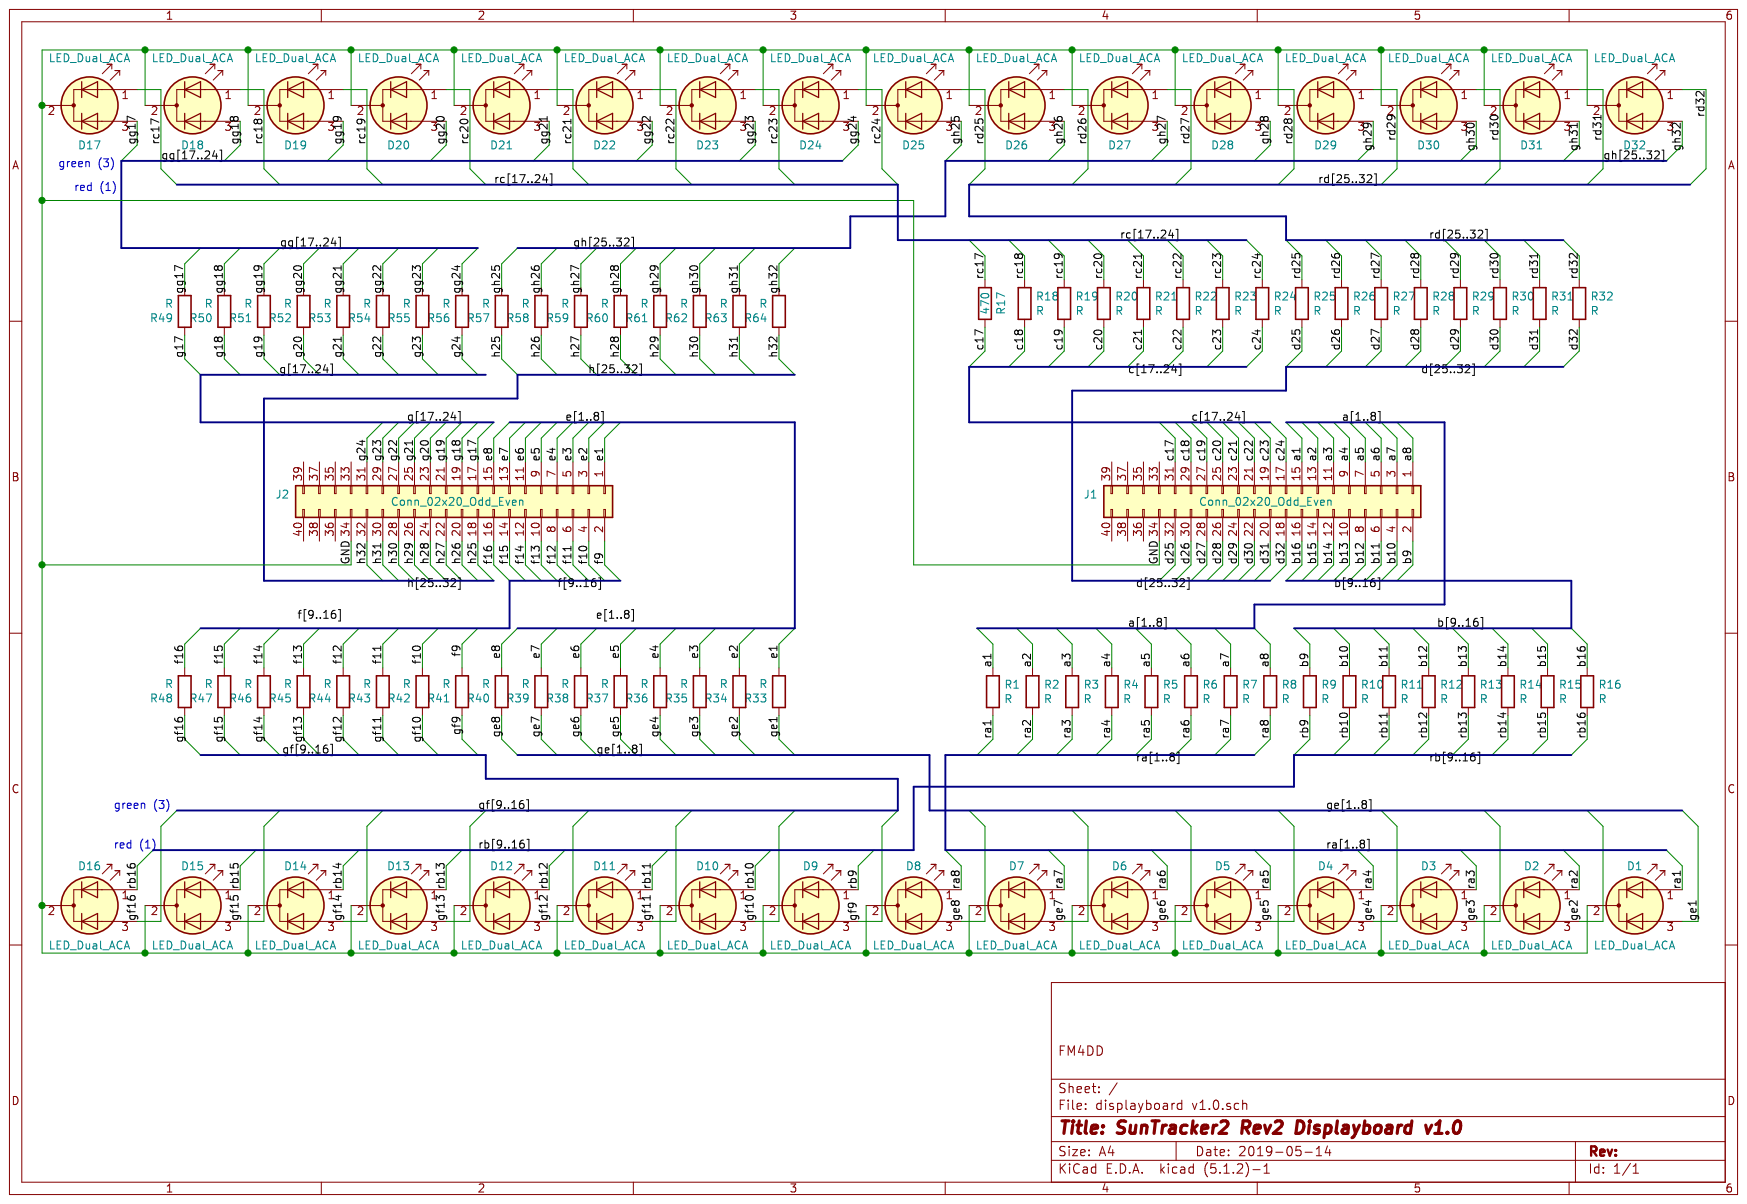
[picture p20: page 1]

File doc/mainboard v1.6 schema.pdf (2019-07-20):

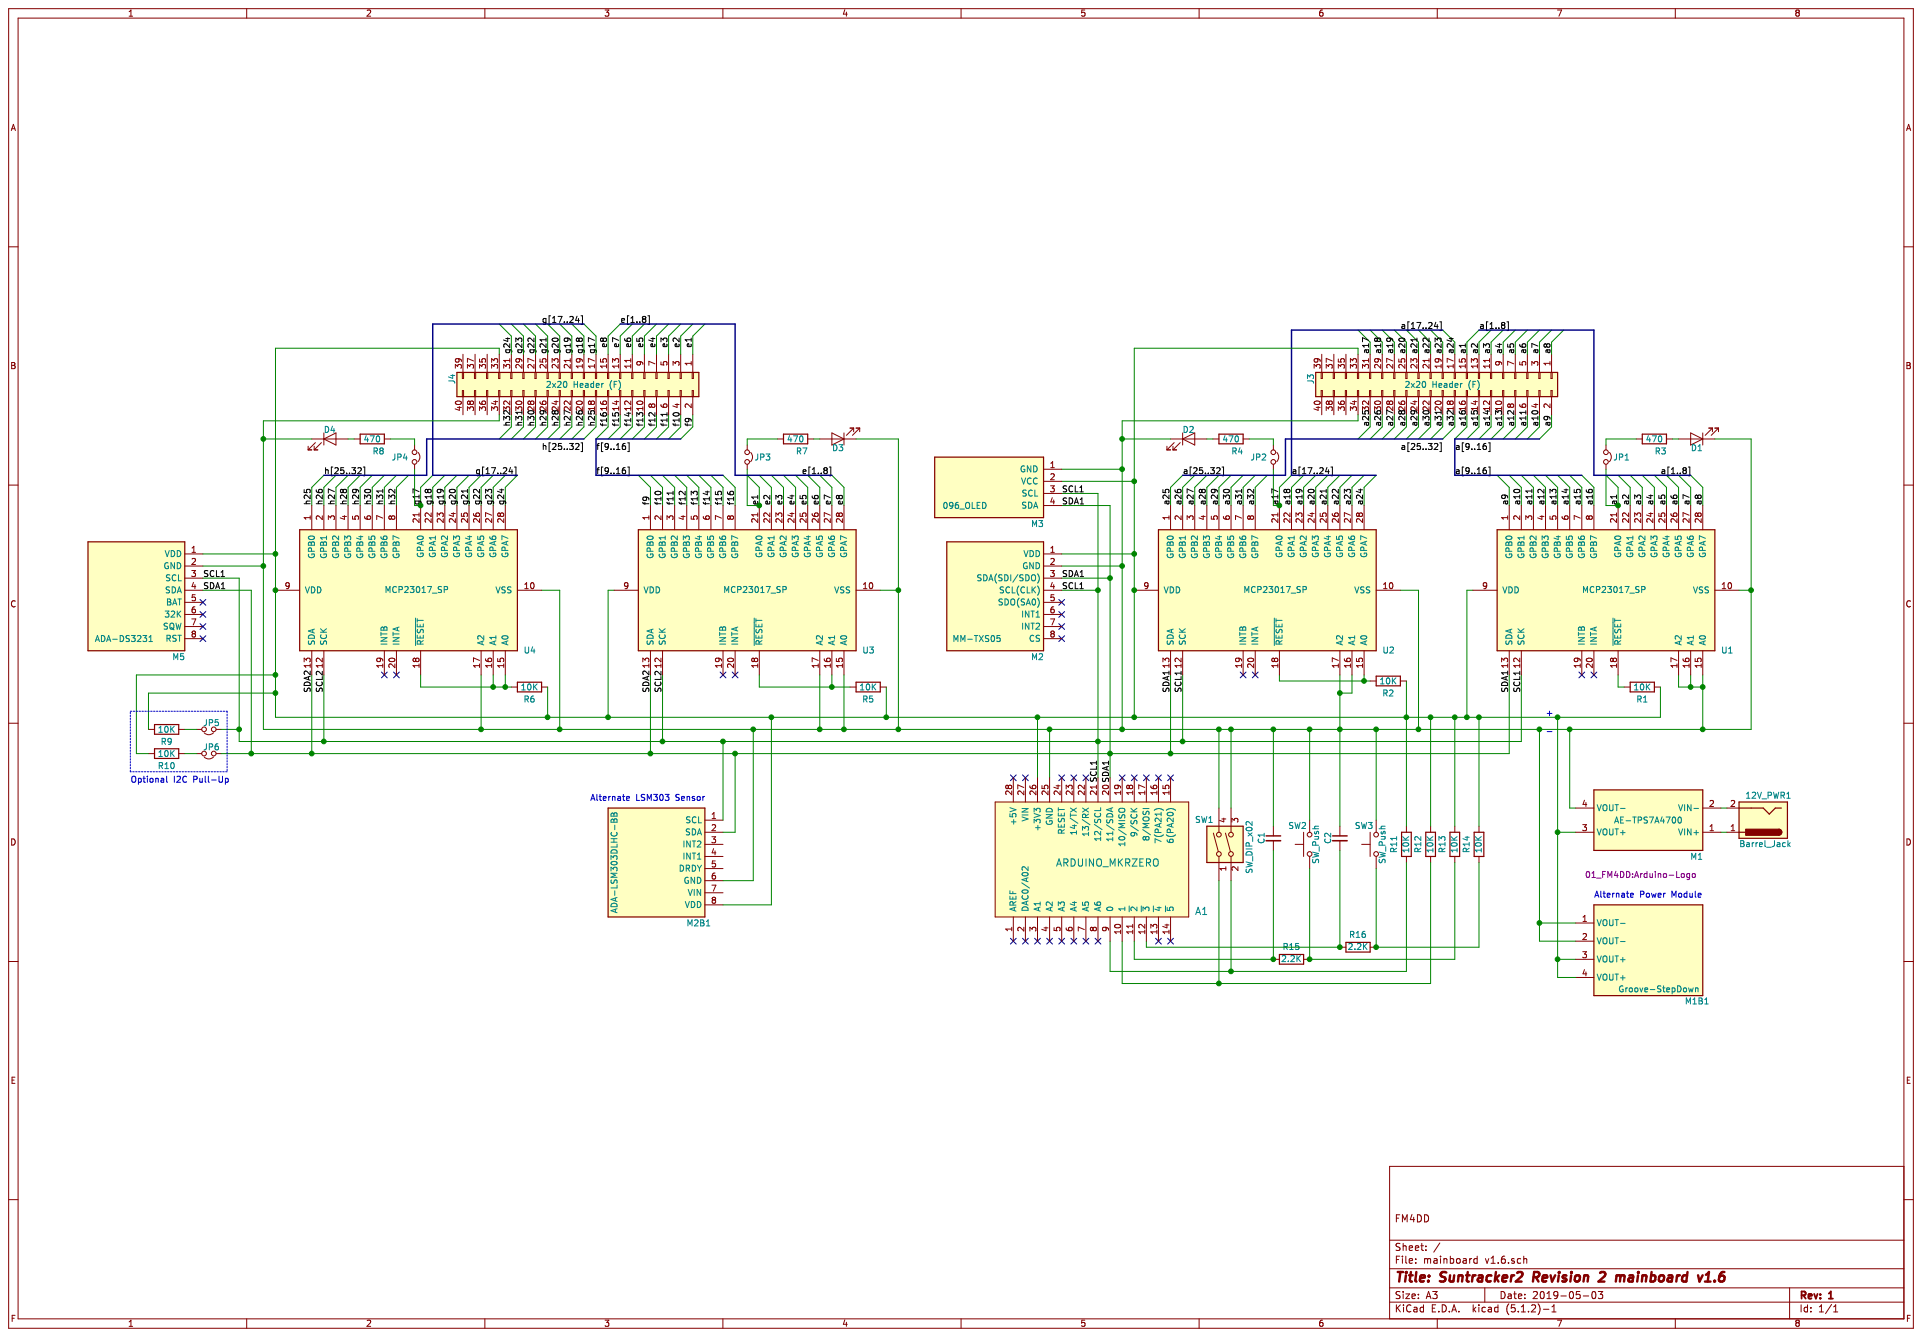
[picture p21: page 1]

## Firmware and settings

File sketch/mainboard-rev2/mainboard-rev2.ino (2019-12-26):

/* ------------------------------------------------- *
 * Suntracker2  mainboard-rev2  June 2019 @ FM4DD    *
 *                                                   * 
 * This code controls Suntracker2 Base-Board v1.6 w. *
 * Displayboard v1.0 for solar azimuth path tracking *
 * Requires suncalc v1.2 generated solar positioning *
 * dataset stored in the root of the MKRZERO MicroSD *
 *                                                   *
 * Always doubleCheck correct sensor HW LSM303D/DLHC *
 * ------------------------------------------------- */
#include <Wire.h>              // Arduino default 12C libary
#include <Arduino.h>           // Arduino default library
#include <SPI.h>               // Arduino default SPI library
#include <SD.h>                // Arduino default SD library
#include "LSM303.h"            // https://github.com/pololu/lsm303-arduino
#include "U8g2lib.h"           // https://github.com/olikraus/u8g2
#include "Adafruit_MCP23017.h" // https://github.com/adafruit/Adafruit-MCP23017-Arduino-Library
#include "uRTCLib.h"           // https://github.com/Naguissa/uRTCLib
#include <avr/dtostrf.h>       // dtostrf float conversion

/* ------------------------------------------------- */
/* DEBUG enables debug output to the serial monitor  */
/* ------------------------------------------------- */
//#define DEBUG

/* ------------------------------------------------- */
/* SD card - Arduino MKRZero onboard card reader     */
/* ------------------------------------------------- */
Sd2Card card;
SdVolume volume;
SdFile root;
const int chipSelect = SDCARD_SS_PIN;
/* ------------------------------------------------- */
/* Magnetic field Sensor                             */
/* ------------------------------------------------- */
LSM303 compass;
/* ------------------------------------------------- */
/* 2x Oled Display - U8G2_R0 = orientation normal    */
/* ------------------------------------------------- */
U8G2_SSD1306_128X64_NONAME_F_HW_I2C oled1(U8G2_R0);

/* ------------------------------------------------- */
/* DS3231 Precision RTC clock                        */
/* ------------------------------------------------- */
uRTCLib rtc;
/* ------------------------------------------------- */
/* 4x IO Expanders for a total of 64 I/O ports       */
/* ------------------------------------------------- */
Adafruit_MCP23017 mcp1;
Adafruit_MCP23017 mcp2;
Adafruit_MCP23017 mcp3;
Adafruit_MCP23017 mcp4;
/* ------------------------------------------------- */
/* Global variable list                              */
/* ------------------------------------------------- */
int8_t hled = 0;             // heading LED (red)
int8_t oldhled = 33;         // 33 > max value 32, indicates "init"
int8_t aled = 0;             // azimuth LED (green)
int8_t oldaled = 33;         // 33 > max value 32, indicates "init"
int8_t rled = 0;             // sunrise LED (red)
int8_t oldrled = 33;         // 33 > max value 32, indicates "init"
int8_t sled = 0;             // sunset LED (red)
int8_t oldsled = 33;         // 33 > max value 32, indicates "init"
uint8_t risehour = 0;        // hour of sunrise
uint8_t risemin = 0;         // minute of sunrise
uint8_t transithour = 0;     // peak altitude hour
uint8_t transitmin = 0;      // peak altitude minute
uint8_t sethour = 0;         // sunset hour
uint8_t setmin = 0;          // sunset minute
float heading;               // North heading
double azimuth;              // sun azimuth angle, north->eastward
double zenith;               // zenith angle, substract from 90 to get altitude
uint16_t riseaz;             // sunrise azimuth, rounded to full degrees
int16_t transalt;            // transit altitude - solar noon peak altitude
uint16_t setaz;              // sunset azimuth, rounded to full degrees
boolean daylight;            // daylight flag, false = night
char lineStr[15];            // display output buffer, 14-chars + \0
char hledStr[5];             // display LED control "-B01"
char dirStr[6];              // display north angle "H263"
char aziStr[6];              // display azimuth angle "A134"
char timeStr[9];             // display time string "HH:MM:SS"
char dateStr[16];            // display date string "YYYY/MM/DD"
char riseStr[16];            // display string "sunrise: 06:45"
char setStr[16];             // display string "sunset:  18:10"
char binfile[13];            // daily sun data file yyyymmdd.bin
char srsfile[13];            // sunrise/sunset file srs-yyyy.bin
const uint8_t dip1  = 0;     // GPIO pin dipswitch-1 on GPIO-0
const uint8_t dip2  = 1;     // GPIO pin dipswitch-2 on GPIO-1
const uint8_t push1 = 2;     // GPIO pin pushbutton-1 on GPIO-2
const uint8_t push2 = 3;     // GPIO pin pushbutton-2 on GPIO-3
const double mdecl = -7.583; // local magnetic declination
uint8_t dippos1 = 0;         // dipswitch 1 position (extra tests)
uint8_t dippos2 = 0;         // dipswitch 2 position (undefined)

/* ------------------------------------------------- */
/* 'arduino logo', 64x32px, XBM format               */
/* ------------------------------------------------- */
static const unsigned char arduLogo[] U8X8_PROGMEM = {
  0x00, 0x00, 0x00, 0x00, 0x00, 0x00, 0x00, 0x00, 0x00, 0x00, 0x00, 0x00, 
  0x00, 0x00, 0x00, 0x00, 0x00, 0xFC, 0x0F, 0x00, 0x00, 0xF0, 0x3F, 0x00, 
  0x80, 0xFF, 0x3F, 0x00, 0x00, 0xFE, 0xFF, 0x00, 0xC0, 0xFF, 0xFF, 0x00, 
  0x80, 0xFF, 0xFF, 0x03, 0xE0, 0xFF, 0xFF, 0x01, 0xC0, 0xFF, 0xFF, 0x07, 
  0xF0, 0x07, 0xF8, 0x07, 0xE0, 0x1F, 0xE0, 0x0F, 0xF8, 0x01, 0xE0, 0x0F, 
  0xF0, 0x07, 0x80, 0x0F, 0xFC, 0x00, 0xC0, 0x1F, 0xF8, 0x01, 0x00, 0x1F, 
  0x7C, 0x00, 0x00, 0x3F, 0xFC, 0x00, 0x00, 0x3E, 0x3E, 0x00, 0x00, 0x7E, 
  0x7E, 0xC0, 0x03, 0x3E, 0x3E, 0x00, 0x00, 0x7C, 0x3F, 0xC0, 0x03, 0x3C, 
  0x1E, 0x00, 0x00, 0xF8, 0x1F, 0xC0, 0x03, 0x7C, 0x1E, 0x00, 0x00, 0xF0, 
  0x0F, 0xC0, 0x03, 0x78, 0x1E, 0xFE, 0x1F, 0xF0, 0x07, 0xFC, 0x3F, 0x78, 
  0x1E, 0xFE, 0x1F, 0xE0, 0x03, 0xFC, 0x3F, 0x78, 0x1E, 0xFE, 0x1F, 0xE0, 
  0x07, 0xFC, 0x3F, 0x78, 0x1E, 0xFE, 0x1F, 0xF0, 0x0F, 0xFC, 0x3F, 0x78, 
  0x1E, 0x00, 0x00, 0xF8, 0x0F, 0xC0, 0x03, 0x78, 0x1E, 0x00, 0x00, 0xFC, 
  0x1F, 0xC0, 0x03, 0x3C, 0x3E, 0x00, 0x00, 0x7E, 0x3E, 0xC0, 0x03, 0x3C, 
  0x3C, 0x00, 0x00, 0x3F, 0x7E, 0xC0, 0x03, 0x3E, 0x7C, 0x00, 0x80, 0x1F, 
  0xFC, 0x01, 0x00, 0x1F, 0xF8, 0x00, 0xC0, 0x0F, 0xF8, 0x03, 0x80, 0x1F, 
  0xF8, 0x03, 0xF0, 0x07, 0xF0, 0x0F, 0xC0, 0x0F, 0xF0, 0x0F, 0xFC, 0x03, 
  0xE0, 0x3F, 0xF0, 0x07, 0xE0, 0xFF, 0xFF, 0x01, 0x80, 0xFF, 0xFF, 0x03, 
  0x80, 0xFF, 0x7F, 0x00, 0x00, 0xFF, 0xFF, 0x01, 0x00, 0xFF, 0x1F, 0x00, 
  0x00, 0xFC, 0x7F, 0x00, 0x00, 0xF8, 0x03, 0x00, 0x00, 0xE0, 0x0F, 0x00, 
  0x00, 0x00, 0x00, 0x00, 0x00, 0x00, 0x00, 0x00, 0x00, 0x00, 0x00, 0x00, 
  0x00, 0x00, 0x00, 0x00, };

/* ------------------------------------------------- */
/* 'day logo', 32x32px, XBM format                   */
/* ------------------------------------------------- */
static const unsigned char dayImg[] U8X8_PROGMEM = {
  0x00, 0x00, 0x00, 0x00, 0x00, 0xC0, 0x03, 0x00, 0x00, 0xE0, 0x07, 0x00, 
  0x00, 0xE0, 0x07, 0x00, 0xE0, 0xC0, 0x03, 0x07, 0xF0, 0x81, 0x81, 0x0F, 
  0xF0, 0x01, 0x80, 0x0F, 0xF0, 0x01, 0x80, 0x0F, 0xE0, 0xE0, 0x07, 0x07, 
  0x00, 0xF8, 0x1F, 0x00, 0x00, 0xFC, 0x3F, 0x00, 0x00, 0xFE, 0x7F, 0x00, 
  0x00, 0x3E, 0x7C, 0x00, 0x0C, 0x1F, 0xF8, 0x30, 0x1E, 0x0F, 0xF0, 0x78, 
  0x3E, 0x0F, 0xF0, 0x7C, 0x3E, 0x0F, 0xF0, 0x7C, 0x1E, 0x0F, 0xF0, 0x78, 
  0x0C, 0x1F, 0xF8, 0x30, 0x00, 0x7E, 0x7E, 0x00, 0x00, 0xFE, 0x7F, 0x00, 
  0x00, 0xFC, 0x3F, 0x00, 0x00, 0xF8, 0x1F, 0x00, 0xE0, 0xE0, 0x07, 0x07, 
  0xF0, 0x01, 0x80, 0x0F, 0xF0, 0x01, 0x80, 0x0F, 0xF0, 0x81, 0x81, 0x0F, 
  0xE0, 0xC0, 0x03, 0x07, 0x00, 0xE0, 0x07, 0x00, 0x00, 0xE0, 0x07, 0x00, 
  0x00, 0xC0, 0x03, 0x00, 0x00, 0x00, 0x00, 0x00, };

/* ------------------------------------------------- */
/* 'night logo', 32x32px, XBM format                 */
/* ------------------------------------------------- */
static const unsigned char nightImg[] U8X8_PROGMEM = {
  0x00, 0x00, 0x00, 0x00, 0x00, 0x00, 0x00, 0x00, 0x00, 0x00, 0x00, 0x00, 
  0x00, 0x00, 0x00, 0x00, 0x00, 0x02, 0x00, 0x00, 0x00, 0x03, 0x00, 0x00, 
  0x80, 0x03, 0x00, 0x00, 0xC0, 0x03, 0x00, 0x00, 0xE0, 0x03, 0x00, 0x00, 
  0xE0, 0x07, 0x00, 0x00, 0xF0, 0x07, 0x00, 0x00, 0xF0, 0x07, 0x00, 0x00, 
  0xF0, 0x0F, 0x00, 0x00, 0xF0, 0x1F, 0x00, 0x00, 0xF8, 0x1F, 0x00, 0x00, 
  0xF0, 0x3F, 0x00, 0x00, 0xF0, 0xFF, 0x00, 0x00, 0xF0, 0xFF, 0x01, 0x00, 
  0xF0, 0xFF, 0x0F, 0x0C, 0xF0, 0xFF, 0xFF, 0x0F, 0xE0, 0xFF, 0xFF, 0x0F, 
  0xE0, 0xFF, 0xFF, 0x07, 0xC0, 0xFF, 0xFF, 0x07, 0x80, 0xFF, 0xFF, 0x03, 
  0x00, 0xFF, 0xFF, 0x01, 0x00, 0xFE, 0x7F, 0x00, 0x00, 0xF8, 0x3F, 0x00, 
  0x00, 0xA0, 0x07, 0x00, 0x00, 0x00, 0x00, 0x00, 0x00, 0x00, 0x00, 0x00, 
  0x00, 0x00, 0x00, 0x00, 0x00, 0x00, 0x00, 0x00, };

/* ------------------------------------------------- */
/* 'ghost logo', 32x32px, XBM format                 */
/* ------------------------------------------------- */
static const unsigned char ghostImg[] U8X8_PROGMEM = {
  0x00, 0x00, 0x00, 0x00, 0x00, 0x00, 0x00, 0x00, 0x00, 0xE0, 0x07, 0x00, 
  0x00, 0xFC, 0x1F, 0x00, 0x00, 0xFE, 0x7F, 0x00, 0x00, 0xFF, 0xFF, 0x00, 
  0x80, 0xFF, 0xFF, 0x00, 0x80, 0xFF, 0xFF, 0x01, 0xC0, 0xFF, 0xFF, 0x01, 
  0xC0, 0xFF, 0xFF, 0x01, 0xC0, 0xC3, 0xC3, 0x03, 0xE0, 0xC3, 0xC3, 0x03, 
  0xE0, 0xC3, 0xC3, 0x03, 0xE0, 0xFF, 0xFF, 0x03, 0xE0, 0xFF, 0xFF, 0x03, 
  0xE0, 0x3F, 0xFE, 0x03, 0xE0, 0x0F, 0xF8, 0x03, 0xE0, 0x07, 0xF0, 0x03, 
  0xE0, 0x07, 0xF0, 0x03, 0xE0, 0xFF, 0xFF, 0x03, 0xE0, 0xFF, 0xFF, 0x03, 
  0xE0, 0xFF, 0xFF, 0x03, 0xE0, 0xFF, 0xFF, 0x03, 0xE0, 0xFF, 0xFF, 0x03, 
  0xE0, 0xFF, 0xFF, 0x03, 0xE0, 0xFD, 0xFE, 0x03, 0xE0, 0xFD, 0xBE, 0x03, 
  0xC0, 0x79, 0xBE, 0x03, 0xC0, 0x78, 0x1C, 0x03, 0x80, 0x30, 0x08, 0x02, 
  0x00, 0x00, 0x00, 0x00, 0x00, 0x00, 0x00, 0x00, };

/* ------------------------------------------------- */
/* 'sunrise logo', 16x16px, XBM format               */
/* ------------------------------------------------- */
static const unsigned char riseImg[] U8X8_PROGMEM = {
  0x00, 0x00, 0x80, 0x00, 0x82, 0x40, 0x84, 0x20, 0x08, 0x10, 0xC0, 0x03, 
  0xF0, 0x0F, 0xFA, 0x5F, 0xF8, 0x1F, 0xFC, 0x3F, 0xFC, 0x3F, 0xFC, 0x3F, 
  0x00, 0x00, 0xFC, 0x3F, 0x00, 0x00, 0xE0, 0x07, };

/* ------------------------------------------------- */
/* 'sunset logo', 16x16px, XBM format                */
/* ------------------------------------------------- */
static const unsigned char setImg[] U8X8_PROGMEM = {
  0x00, 0x00, 0x00, 0x00, 0x00, 0x0F, 0xC0, 0x03, 0xE0, 0x01, 0xF0, 0x00, 
  0x78, 0x00, 0x78, 0x00, 0x78, 0x00, 0xF0, 0x01, 0xE0, 0x0F, 0xFC, 0x3F, 
  0x00, 0x00, 0xFC, 0x3F, 0x00, 0x00, 0xE0, 0x07, };
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
void loop() {
  /* ------------------------------------------------- */
  /* Aquire time                                       */
  /* Every new minute read solar position data         */
  /* ------------------------------------------------- */
  rtc.refresh();
  if(rtc.second() == 0) {
    if(rtc.minute() == 0) {
      snprintf(binfile, sizeof(binfile), "20%d%02d%02d.BIN", 
                rtc.year(),rtc.month(),rtc.day());
      if(rtc.day() == 1) {
        snprintf(srsfile, sizeof(srsfile), "SRS-20%d.BIN", 
                rtc.year());
      }
      get_suntime(srsfile);
      snprintf(riseStr, sizeof(riseStr), "rise %02d:%02d %03d",
               risehour,risemin, riseaz);
      snprintf(setStr, sizeof(setStr), "set  %02d:%02d %03d",
               sethour, setmin, setaz);
    }
    solar_position(binfile);
    display_daysymbol(oled1);
  }
  /* ------------------------------------------------- */
  /* Show time on OLED                                 */
  /* ------------------------------------------------- */
  snprintf(dateStr, sizeof(dateStr), "20%d/%02d/%02d",
  rtc.year(),rtc.month(),rtc.day());
  snprintf(timeStr, sizeof(timeStr), "%02d:%02d:%02d",
  rtc.hour(),rtc.minute(),rtc.second());
  oled1.setFont(u8g2_font_t0_17_mr);
  oled1.setCursor(0, 47);
  oled1.print(dateStr);
  oled1.setCursor(0, 63);
  oled1.print(timeStr);

  /* ------------------------------------------------- */
  /* Aquire compass sensor data                        */
  /* ------------------------------------------------- */
  compass.read();
  
  /* ------------------------------------------------- */
  /* If the sensor board orientation is unaligned, set */
  /* compass.heading((LSM303::vector<int>){0,1,0}) for */
  /* pointing along the Y-axis for example. Remove if  */
  /* the X-axis is the point of reference on a LSM303D */
  /* ------------------------------------------------- */
  /* Because magnetic north != real north, we adjust:  */
  /* Calculate magnetic declination and convergence    */
  /* to determine true North from magnetic North       */ 
  /* https://www.ngdc.noaa.gov/geomag/WMM/soft.shtml   */
  /* ------------------------------------------------- */
  if(compass.getDeviceType() == 3) heading = compass.heading() + mdecl;
  if(compass.getDeviceType() == 2) heading = compass.heading((LSM303::vector<int>){1,0,0}) + mdecl;
  
  /* ------------------------------------------------- */
  /* print North heading to OLED                       */
  /* ------------------------------------------------- */
  snprintf(dirStr, sizeof(dirStr), "H%03d", (int)round((heading) * 10 / 10.0));
  oled1.setFont(u8g2_font_inr19_mr);
  oled1.drawStr(0,26, dirStr);

  /* ------------------------------------------------- */
  /* Convert heading angle to LED range value (0..32)  */   
  /* ------------------------------------------------- */
  hled = (uint8_t)round((heading / 11.25) * 10 / 10.0);
  aled = (uint8_t)round((azimuth / 11.25) * 10 / 10.0);
  rled = (uint8_t)round((riseaz / 11.25) * 10 / 10.0);
  sled = (uint8_t)round((setaz / 11.25) * 10 / 10.0);
  /* ------------------------------------------------- */
  /* If 32 is returned, it should roll over to 0       */   
  /* ------------------------------------------------- */
  if(hled > 31) hled = 0;
  if(aled > 31) aled = 0;
  if(rled > 31) rled = 0;
  if(sled > 31) sled = 0;
  /* ------------------------------------------------- */
  /* Because LED-1 is 90 degrees offset, we compensate */
  /* ------------------------------------------------- */
  hled = hled + 24; if(hled > 31) hled = hled - 32;
  /* ------------------------------------------------- */
  /* Reverse counting to keep the LED aligned to North */
  /* ------------------------------------------------- */
  hled = 32 - hled; if(hled > 31) hled = 0;
  /* ------------------------------------------------- */
  /* Remaining LED follow heading                      */
  /* ------------------------------------------------- */
  aled = hled + aled; if(aled > 31) aled = aled - 32;
  rled = hled + rled; if(rled > 31) rled = rled - 32;
  sled = hled + sled; if(sled > 31) sled = sled - 32;

#ifdef DEBUG
   var2serial();
#endif 

  /* ------------------------------------------------- */
  /* Set heading LED                                   */
  /* ------------------------------------------------- */
  if (hled != oldhled) {
    if(oldhled < 16) mcp1.digitalWrite(oldhled, LOW);
    else if(oldhled < 32) mcp2.digitalWrite((oldhled-16), LOW);
    if(hled < 16) mcp1.digitalWrite(hled, HIGH);
    if(hled > 15) mcp2.digitalWrite((hled-16), HIGH);
    display_hdgled(oled1, oldhled, hled);
    oldhled = hled;
  }
  
  /* ------------------------------------------------- */
  /* Set azimuth LED                                   */
  /* ------------------------------------------------- */
  if (aled != oldaled) {
    if(oldaled < 16) mcp3.digitalWrite(oldaled, LOW);
    else if(oldaled < 32) mcp4.digitalWrite((oldaled-16), LOW);
    if(aled < 16) mcp3.digitalWrite(aled, HIGH);
    if(aled > 15) mcp4.digitalWrite((aled-16), HIGH);
    oldaled = aled;
  }

  /* ------------------------------------------------- */
  /* Set sunrise LED                                   */
  /* ------------------------------------------------- */
  if (rled != oldrled) {
    if(oldrled < 16) mcp1.digitalWrite(oldrled, LOW);
    else if(oldrled < 32) mcp2.digitalWrite((oldrled-16), LOW);
    if(rled < 16) mcp1.digitalWrite(rled, HIGH);
    if(rled > 15) mcp2.digitalWrite((rled-16), HIGH);
    oldrled = rled;
  }
  
  /* ------------------------------------------------- */
  /* Set sunset LED                                   */
  /* ------------------------------------------------- */
  if (sled != oldsled) {
    if(oldsled < 16) mcp1.digitalWrite(oldsled, LOW);
    else if(oldsled < 32) mcp2.digitalWrite((oldsled-16), LOW);
    if(sled < 16) mcp1.digitalWrite(sled, HIGH);
    if(sled > 15) mcp2.digitalWrite((sled-16), HIGH);
    oldsled = sled;
  }

  oled1.updateDisplay();
  delay(50);
}

/* ------------------------------------------------- */
/* get solar postion record for current time.        */
/* ------------------------------------------------- */
void solar_position(char *file) {
  uint8_t linebuf[19];
  File bin = SD.open(file);
  while (bin.available()) {
    bin.read(linebuf, sizeof(linebuf));
    if(linebuf[0] == rtc.hour() && linebuf[1] == rtc.minute()) {
      memcpy(&azimuth, &linebuf[3], sizeof(double));
      memcpy(&zenith, &linebuf[11], sizeof(double));
      if(linebuf[2] == 1) daylight = 1;
      else daylight = 0;
      break;
    }
  }
  bin.close();
}

/* ------------------------------------------------- */
/* get sunrise/transit/sunset record for current day */
/* ------------------------------------------------- */
void get_suntime(char *file) {
  uint8_t linebuf[14];
  File bin = SD.open(file);
  while (bin.available()) {
    bin.read(linebuf, sizeof(linebuf));
    if(linebuf[0] == rtc.month() && linebuf[1] == rtc.day()) {
      risehour=linebuf[2];
      risemin=linebuf[3];
      memcpy(&riseaz, &linebuf[4], sizeof(uint16_t));
      transithour=linebuf[6];
      transitmin=linebuf[7];
      memcpy(&transalt, &linebuf[8], sizeof(int16_t));
      sethour=linebuf[10];
      setmin=linebuf[11];
      memcpy(&setaz, &linebuf[12], sizeof(uint16_t));
      break;
    }
  }
  bin.close();
}

/* ------------------------------------------------- */
/* led_lightcheck() LED on/off tests for all 4 units */
/* ------------------------------------------------- */
void led_lightcheck() {
  /* ------------------------------------------------- */
  /* Blink all ports. 0xFFFF lights both GPIOA and B.  */
  /* Set 0xFF only lights GPIOA, 0x00FF lights only B  */
  /* ------------------------------------------------- */
  mcp1.writeGPIOAB(0xFFFF);
  delay(500);
  mcp1.writeGPIOAB(0x00);
  mcp2.writeGPIOAB(0xFFFF);
  mcp3.writeGPIOAB(0xFFFF);
  delay(500);
  mcp2.writeGPIOAB(0x00);
  mcp3.writeGPIOAB(0x00);
  mcp4.writeGPIOAB(0xFFFF);
  delay(500);
  mcp4.writeGPIOAB(0x00);
}
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

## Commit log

2019-12-14 Add demo sketches and board manual DE
    [20191214 Suntracker2r2 enclosure v1.0.dxf, 20191214 suntracker2r4-enclosure-stands-v1.0.dxf]
2020-04-12 update repo
    [20191214 Suntracker2r2 enclosure v1.0.dxf, 20191214 suntracker2r4-enclosure-stands-v1.0.dxf]
